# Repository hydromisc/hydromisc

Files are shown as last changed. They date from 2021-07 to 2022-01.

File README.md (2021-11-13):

# Hydromisc

This is a single PCBA with all the necessary I/O to automate a typical
small to mid-size hydroponic grow, controllable over Wi-Fi. It may also
be suitable for aquariums, ponds, or any other biological or chemical
process involving water treatment. Inputs and outputs include:

* 8x 12 V, 1 A outputs, intended for solenoid valves (but usable for other
actuators too)
* 6x 12 V, 0.5 A ouputs, intended for pumps, with current monitoring
* 4x 12 V, 0.25 A outputs, intended for peristaltic dosing pumps, with analog
voltage control
* 2x direct interfaces to a pH probe or other ion-selective electrode
* 2x direct interfaces to an EC (electrical conductivity) probe, reading around 1000 uS
* 2x direct interfaces to a resistive sensor (thermistor, photoresistor,
etc.), reading around 10k
* 2x digital interface to a temperature and humidity sensor
* 2x digital interface to a strain gauge (to measure weight or pressure)

Typical hydroponic practice is to maintain the solution at a target EC and
pH, using EC as a proxy for fertilizer concentration and dosing acid or
(rarely) alkali to adjust pH. I'm using this board now to control injector
pumps in a drain-to-waste system, open-loop with manual adjustment, and
also to maintain closed-loop EC and pH in a recirculating system.

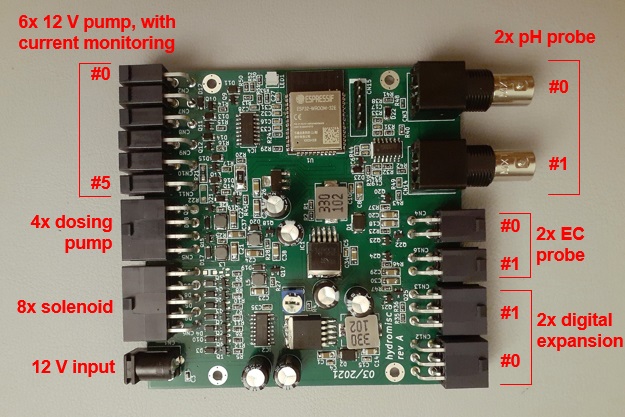
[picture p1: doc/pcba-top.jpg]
all connectors labeled


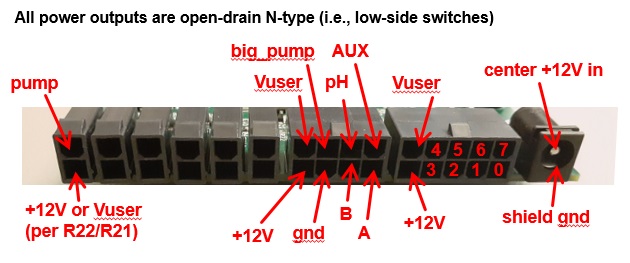
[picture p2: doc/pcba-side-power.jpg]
power side pinout


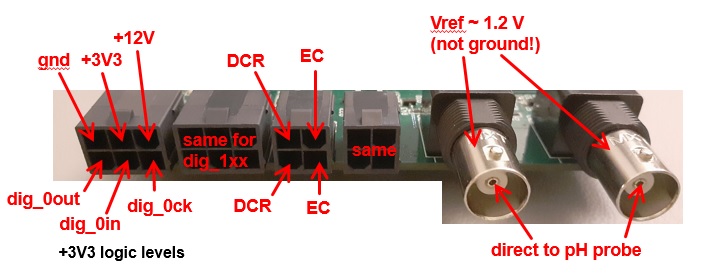
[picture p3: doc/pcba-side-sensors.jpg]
sensor side pinout


## Firmware

The board is managed by an ESP32. Install the
[ESP-IDF](https://github.com/espressif/esp-idf) framework from Espressif,
and build and load the firmware from an ESP-IDF command prompt.

The board is a Wi-Fi client. The name and password for its access point
must be compiled in to the program, in Espressif's usual way, with `idf.py
menuconfig`. The board will automatically get an IP address over DHCP,
so you'll probably want to configure your router or other DHCP server to
assign a static IP based on the MAC address. The MAC address is unique
per board, since that's serialized in the ESP32 module.

The current firmware implements a simple interface to read the sensors
and write the actuators over http. I'm currently sequencing everything with
some shell scripts initiated by cron jobs on a Raspberry Pi, which invoke
curl to command this board. Any device and programming language capable of
making http requests could be used, though.

The outputs are described as "solenoid", "pump", and "dosing pump",
because that's the purpose for which I'm personally using them, and the
present interface is named around that model. They can of course be
used for other types of load too. The software interface is easily
extended if the present commands are inadequate or too confusingly-named.

    $ curl 'http://hydromisc/solenoid?k=3&t=20&'\
    'dosingA=90&dosingB=90&dosingPh=210&dosingAux=0'
    { "result": "solenoiding" }

Solenoid output k is energized for t seconds. For the same period,
the four dosing pumps are also energized, with the respective duty
cycles from 0 (off) to 254 (full on, ~12 VDC). The voltage applied to
the dosing pump is very roughly linear in duty cycle, but both that map
and the map from voltage to speed are quite inexact. If you're closing
the loop (e.g., dosing acid to achieve a particular pH), then this may
not matter, since your control loop will automatically correct that. If
accuracy is important, then the pump should be calibrated, for example
by measuring the amount of liquid dispensed using a graduated cylinder
or weighing scale.

The solenoid output is powered for three seconds after the pumps stop.
This is to avoid closing the solenoid valves with pressure in the system,
since the pumps will continue to operate briefly after losing power. If
the dosing pumps feed directly into a single reservoir, then this and
everything else about the solenoids may be ignored.

    $ curl 'http://hydromisc/pump?k=4&t=15'
    { "result": "pumping" }

Pump output k is energized for t seconds. The measured current (up to about
500 mA) is recorded.

    $ curl 'http://hydromisc/current'
    { "result": "current","current": [ 71, 65, 74, 69, 78, 74, 80, 73, 63,
    73, 65, 68, 74, 64, 60 ] }

The current from the most recent /pump is reported, in units of milliamps
at one sample per second. If this hasn't yet completed, a full-length
trace is reported but future samples are 0.

    $ curl 'http://hydromisc/stop'
    { "result": "stopping" }

All (solenoid, pump, dosing pump) outputs are de-energized immediately.

    $ curl 'http://hydromisc/sensors'
    { "result": "sensors", "ec0": 984, "ec1": 47, "ph0": 41, "ph1": -320,
    "dcr0": 210000, "dcr1": 210000, "temp0": 25.7, "humidity0": 54.0,
    "temp1": -9999.9, "humidity1": -9999.9, "sg0": 0, "sg1": -1 }

All sensors are measured and reported.

The pH electrode voltage is returned in millivolts, and your software
must convert to pH. To a first order, the map from voltage to pH is
linear, with zero volts corresponding to pH = 7.0, and a slope around
59 mV/unit around room temperature (which may be calculated using the
Nernst equation).

You should calibrate by measuring the voltage in two solutions of known
pH (e.g., 4.0 and 6.9), and interpolating linearly between the two. For
example:

    const V69 = 8;      // millivolts in pH 6.9 calibration buffer
    const V40 = -152;   // millivolts in pH 4.0 calibration buffer

    const slope = (V69 - V40)/(6.9 - 4.0);

    let ph = 6.9 + (resp.ph0 - V69)/slope;

Your software must also correct for temperature if desired; though in
typical hydroponic applications, the pH is close enough to neutral that
it doesn't matter too much. To a first order, the slope changes with
temperature but the offset does not, so the tempco is very small when the
output voltage is small.

Other ion-selective electrodes (e.g., for nitrate, potassium, etc.) should
also work with this interface circuit. Consult the electrode documentation
for the calibration procedure, which should be specified in terms of
millivolts from the meter. The reference electrode would need to go to
the BNC shell (Vref ~ 1.2 V), not ground.

EC is returned directly in microsiemens, uS. For example, a resistance
of 1kohm is equal to 1000 uS. Your software must convert based on the
cell dimensions (to convert from uS to uS/cm; a cell constant of 1 cm
is typical so that may be trivial), and also perform any temperature
compensation if desired. If you already have a different EC meter,
then you can use that with a sample of hydroponic solution to transfer
calibration. If not, then you can calibrate in a solution of 1000 mg/L
sodium chloride (table salt), which has conductivity of 2000 uS/cm at
25 degrees Celsius.

In concept, any two wires the right length and distance apart (e.g.,
on the order of 1 cm) could be immersed in solution, and could serve
as your EC electrode. You may prefer to buy a purpose-built electrode,
though. That may have a plastic sheath that protects the electrodes
from mechanical damage with a slit to avoid trapping air bubbles. The
electrode material should also have good electrochemical properties.
Inexpensive electrodes will generally use stainless steel. The most
expensive electrodes will use a thin coating of platinum black, which
reduces error by reducing the series resistance due to electrode
polarization. Either is likely fine in practice.

Electrodes may also be inserted into media, in which case they measure
a product of the solution EC and the media water content. An EC channel
can also be used as a binary liquid level sensor, by placing the
electrodes just below the threshold level. In such use, take care that
the electrodes are far enough apart that surface tension can't hold
a drop of solution even when they aren't immersed.

To measure water (or other) temperature, you can use a thermistor. Some
EC or pH probes will have a thermistor integrated in the probe,
or you can buy one separately. The resistance of that thermistor
(or any other resistive sensor) is returned directly in ohms. Your
software must convert to temperature. For a typical NTC thermistor,
the logarithm of the resistance is proportional to the reciprocal of
absolute temperature. For example:

    // we calibrated at 22 degrees Celsius, and measured 10435 ohms
    const calLogR = Math.log(10435);
    const calTemp = 22;

    // from some random NTC thermistor datasheet, or you could also do a
    // two-point calibration
    const slope = 0.0002578;

    let Tinv = 1/(273 + calTemp) + slope*(Math.log(resp.dcr0) - calLogR);
    let T = 1/Tinv - 273;

I'm also using that interface with a photoresistor to count hours of sun,
though I'm doing a simple binary threshold (to distinguish direct sun
vs. shade) and not a full continuous calibration.

To measure air temperature and humidity, connect an AM2301 on either 2x3
position connector to ground (black), +3V3 (red), and DIG_xOUT (yellow).
Temperature is returned in degrees Celsius, and humidity in percent RH.
A pull-up resistor from red to yellow may be required if the wires are long,
since we otherwise just get the ESP32's on-chip pull-up.

To measure a strain gauge, connect an HX710 to ground, +3V3, DIG_xCK
(SCK), and DIG_xIN (DOUT). The result is returned in raw ADC units,
which you can calibrate to force or pressure with a linear offset and
scale. I use this to measure liquid level with a "bubbler" system,
measuring the hydrostatic pressure in an air-filled tube at the bottom
of the tank. (It's necessary to bubble a slow trickle of air through the
tube, or else tiny leaks will cause it to eventually fill with water; but
since I'm already aerating my tanks, that just takes a tee and a needle
valve. Such systems are common in process industries, crude but cheap
and reliable. My system is okay but not great, since the pressure sensor
has a large tempco. I used an additional AM2301 very close to the sensor
to compensate, but there's still an inch or so worth of residual error.)

You can simultaneously connect an HX710 and an AM2301 to the same
2x3 connector, since they use different data pins.

    $ curl 'http://hydromisc/conf?dosingAPhase=63&dosingBPhase=4032&'\
    'dosingPhPhase=4095&dosingAuxPhase=4095&runBigPump=1'
    { "result": "configured" }

By default, the dosing pumps run continuously during a /solenoid call.
Here they can also be configured to run intermittently, in 100 ms
intervals on a 12-interval (1.2 s) period. The operation of each dosing
pump may be specified here as a bitmap, 12 bits as a decimal number. For
example, the decimal number 63 is equal to 12'b000000111111, so dosing
pump A is on with duty cycle 1/2, 600 ms on followed by 600 ms off. The
decimal number 4032 is equal to 12'b111111000000, so dosing pump B is
also on with duty cycle 1/2 but with opposite phase.

When peristaltic pumps are used as fertilizer injectors, this intermittent
operation can achieve lower injection rates than can be reliably achieved
with low pump voltage (since the transfer characteristic from voltage to
flow varies a lot at low voltage). The phase may be chosen to minimize
risk of mixing before dilution.

By default, the output BIG_PUMP is energized during a /solenoid call. This
may be disabled by setting runBigPump=0.

## Getting Hardware

For the moment, this hardware isn't commercially available in assembled
form. (That may change, since this is open hardware that anyone can build
and sell; I'll add links if and when it does.) You'll therefore have to
buy the bare PCB and parts kit, and assemble yourself. This PCBA has no
leadless or fine-pitch components, so it can be hand-assembled with a
soldering iron and moderate skill.

Note that rev A of the PCB has one major erratum, a missing pull-up on
ESP32_EN, plus some smaller issues that degrade analog performance. I've
corrected these in rev C, which is the head revision in git, but never
actually built and tested that. So it's possible there's still a mistake,
though the risk should be small. Full details of the changes are in
[board/README.md](https://github.com/hydromisc/hydromisc/blob/master/board/README.md).

Total cost to build one board is around:

Item | Cost
----------- | --------------
bare PCB, PCBWay | $30
components, Digi-Key | $60

All connectors are Molex Mini-Fit Jr., a very popular series. It's
possible to solder the cable-end connectors rather than crimping
them, but not recommended. The official crimp tool is expensive. I've used
a third-party "SN-28B", which isn't actually designed for that family
but is cheap and barely adequate, if I crimp first with the largest
die and then again with the middle one.

To program the board, use any USB-to-serial adapter with +3V3 logic levels,
for example an FT232R. Take care that you need access to RTS, which some
such boards and cables don't break out. On CN15, connect:

* ground to ground
* +3V3 to nothing
* USBSER_RX to ESP32_TXD0
* USBSER_TX to ESP32_RXD0
* USBSER_DTR to ESP32_IO0
* USBSER_RTS to ESP32_EN

Program with `idf.py flash` in the usual way. Disconnect digital expansion
devices when programming, since they can interfere.

For complete automated control of EC and pH, you might add:

Item | Cost
----------- | --------------
pH electrode, Yieryi | $15
EC electrode | $15
3x aquarium-type dosing pump | $30
water fill solenoid valve | $15

See my brief
[review of the sensors and actuators now cheaply available on Chinese markets](https://github.com/hydromisc/hydromisc/blob/master/doc/sensors-actuators.md).

Then you might periodically (e.g., minutes to hours) measure EC and pH
with /sensors. You could also monitor solution level, using another EC
electrode positioned high in the tank or using a float switch. The board
has no binary digital inputs, but the DC resistance or EC channels work
with switch contacts too. Then using /solenoid, you could add water,
fertilizer, and acid as required to maintain desired liquid level,
EC and pH.

You would typically aim to keep pH constant, for example with simple
hysteretic (bang-bang) control--add phosphoric if the pH is too high,
or add potassium carbonate if the pH is too low, with a significant
deadband (e.g., 0.5 units) so the acid and alkali don't fight it out
and leave too much potassium phosphate in the solution. In most cases
the alkali would actually be unnecessary, since the natural alkalinity
of the water supplies all necessary pH rise. That's the reason why only
one dosing pump channel is labeled "pH", though the AUX channel could
be used for alkali if desired.

Control of EC is more complicated, since unwanted ions (e.g., sodium
and chloride) will accumulate over time in the solution. So constant EC
probably means rising unwanted ions but falling NPK, and will eventually
result in deficiency. If you maintain constant EC, then you'll need to
change the reservoir often. You can waste less water by allowing slow
rise, though managing that without detailed water analyses is somewhat
uncertain. In all cases, fertilizer should be dosed in a way that doesn't
risk mixing of Part A and Part B before they're fully diluted, to avoid
precipitation (nutrient lockout) from the reaction between calcium ions
and phosphate or sulfate. For example, dose at opposite ends of the tank,
or allow sufficient time to mix between parts.

Of course more complicated automation is possible too. For example, this
board could manage multiple reservoirs simultaneously, or sense EC and
pH both in the reservoir and in returning solution from NFT channels, or
manage fertilizer injectors for a drain-to-waste system. The large number
of inputs and outputs is intended to provide flexibility to interface to
almost any conceivable system's sensors and actuators, with the automated
behavior determined by the software that commands this board.

## Circuit Explanation

Input power is +12 V, which feeds the power outputs directly. It also
feeds a buck converter that makes our +5V, and a buck converter that
makes Vuser, arbitrarily adjustable with a trimpot. An LDO makes +3V3
from +5V, and all our logic runs from that.

The ESP32 is a module with integrated antenna. It would be better for
the antenna tuning if the board outline had a cutout for that, but I
preferred mechanical robustness over antenna range. The ESP32 drives
two 8-bit serial-input, parallel-output shift registers, which function
as GPIO expanders and gate drivers for the pump and solenoid power
FETs. Max current for the solenoid outputs is determined by thermals due
to I^2\*Rdson. I haven't measured that temperature rise, but something
around an amp should be quite safe. Max current for the pump outputs is
determinated by the 2.2 ohm low-side current-sense resistor, and could
be increased by decreasing that.

The dosing pump gates are driven directly by ESP32 PWM outputs. A
series LC makes the negative-ground equivalent of a buck converter
on those outputs, enabling us to drive the dosing pumps not with PWM
but with a programmable DC voltage. This decreases radiated emissions,
and provides something like a constant voltage output as long as the
converter remains in continuous conduction.

The pump outputs return their ground current through a current-sense
resistor, and an ESP32 ADC channel measures the voltage across that. This
enables us to measure pump current. For example, if pump current
is much higher when pumping water than when pumping air, this lets us
measure the volume of water pumped out of a tray by measuring when the
pump current drops. The current can also be used for health monitoring, to
confirm the pump is actually connected and operating with expected load.

A pH electrode develops a voltage around 0 V at pH 7, plus or minus
roughly 59 mV per pH unit at room temperature. Its output impedance may be
many megohms, so we measure that voltage with an electrometer-type opamp,
with femtoamp input current. To mitigate leakage resistance across our
PCB (e.g., due to ionic contamination from flux residue), we surround
the sensitive trace with a driven shield held at the same voltage as that
sensitive node. I've seen no trouble due to leakage even without cleaning
flux, though I live in a dry climate and it would be better to clean that.

Since the pH electrode voltage may be positive or negative and we don't
have a negative supply, we connect its "ground" to a 1.2 V reference. This
means that any electrical connection between our circuit ground and
the solution being measured will result in an incorrect measurement,
though the shunt regulator that generates that rail can survive a short
to ground without damage. The shield of the BNC connectors is 1.2 V,
not ground. As long as the board is powered from an isolated power supply
(for example, a typical mains-operated power brick), no further attention
should be required; but take care not to de-isolate it, for example by
attaching board ground to any metal that touches the solution.

Even with DC isolation, a significant 60 Hz (or 50 Hz) component may
be present on the pH probe voltage. If this saturates the front-end
amplifier, then no subsequent low-pass could recover the correct DC
voltage. We address this with a capacitor across the pH probe. The
resulting low-pass time constant is poorly-controlled, since it's a
function of the probe output resistance.  That's fine in practice though,
since pH shouldn't change significantly over any timescale faster than
minutes.

We pull both sides of the EC electrode up to +3V3 through 1k
resistors, so they both rest at +3V3 with respect to circuit ground, 0 V
differential. To measure EC, we pull one side to ground through an n-FET,
and then measure the voltage of the other, making a voltage divider
between the known 1k and the unknown resistance under test. We then
repeat the process for the other side, restoring zero DC voltage across
the electrode to avoid polarization. The EC electrode is also AC-coupled
through 22 uF ceramic capacitors, guaranteeing zero DC voltage even if
the software misbehaves or the resistors don't perfectly match and, more
importantly, presenting high imepedance at DC so the EC electrode doesn't
short out a pH electrode immersed in the same sample cup. Assuming EC
around 2 mS/cm and cell constant around 1 cm, we get a high-pass time
constant around 4 ms, which is much slower than our measurement period
of ~500 us. Electrolytic capacitors can't be used for that AC-coupling,
since the leakage current is too high.

A similar approach may be used to measure EC with almost
any microcontroller and no additional components beyond the
reference resistors and AC-coupling capacitors, by configuring that
microcontroller's I/O pin as an output low to ground it. I chose to use
the external FETs here because I'd run out of microcontroller pins, and
because the lower and more consistent Rdson improves accuracy at high EC
(since that appears in series with the resistance under test).

## Information Security

None whatsoever. Use this only behind a firewall (like a typical
residential NAT router), on a network with trusted users only. If you
need remote access, expose it through a properly-secured jump box or VPN,
not directly.

## Warranty and Life Safety

THERE IS NO WARRANTY FOR THIS SOFTWARE OR HARDWARE, TO THE EXTENT
PERMITTED BY APPLICABLE LAW. WE PROVIDE THE SOFTWARE OR HARDWARE "AS IS"
WITHOUT WARRANTY OF ANY KIND, EITHER EXPRESSED OR IMPLIED, INCLUDING,
BUT NOT LIMITED TO, THE IMPLIED WARRANTIES OF MERCHANTABILITY AND FITNESS
FOR A PARTICULAR PURPOSE.

DO NOT USE THIS SOFTWARE OR HARDWARE IN SITUATIONS WHERE ITS FAILURE COULD
RESULT IN DANGER TO HUMAN LIFE. For example, don't dose concentrated acid
and rely on correct operation of this board to safely dilute it--instead
dose a higher volume of less concentrated acid, or use safer chemistry
(monopotassium phosphate, etc.). Also think carefully about the risk of
overflowing water, dead plants or fish, and other damage, and don't rely
on software to prevent it.

## License

The firmware is licensed under the GPLv3 or later. The legal framework
for open hardware is poorly-established, but you may build and sell, give
away, or otherwise transfer any number of hydromisc boards, provided that:

* any software loaded on the board is free software (as defined by
any OSI-approved license), and that software is not intended primarily
as a bootloader or other tool to load, program, or otherwise enable use
of non-free software; and

* you do not falsely claim ownership of the design, or any affiliation
with this project beyond your permission to build boards per above.

## Next steps

For now, this project is useful only to people with sufficient programming
skill to build and load the firmware, and to use the http interface
above. For future, it would be nice to:

* Integrate with existing control software (Mycodo, home automation packages,
etc.)

* And/or, add logic on the ESP32 itself for timed irrigations and
closed-loop dosing based on measured pH and EC, to allow this board
to work standalone with no need for the network except for initial
configuration. Firmware to log and graph (as a web page) sensors over
time would also be helpful in standalone use.

* Add a friendly mode to configure Wi-Fi settings, since those currently
must be compiled in. For example, if some combination of pins is jumpered
at startup, appear as a Wi-Fi access point to which the user can connect
and provide the real access point name and password. Then save those
credentials in flash, and use them after reset.

* Clean up how concurrency is managed in the firmware. The present code
seems to work, but it's a lazy hack that's hard to analyze for races.

I might eventually do some of that work myself, but I have limited time
and welcome other contributors. Please feel free to use GitHub issues to
discuss potential new features or anything else.

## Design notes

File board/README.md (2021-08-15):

There are three revisions of the PCB:

* rev A - I built this, and it works except that I forgot the pull-up on
ESP32_EN. Solder a 10k resistor from ESP32_EN to +3V3 (for example, near
CN15), or else the ESP32 module won't start when the programmer is
disconnected.

* rev B - This adds the missing pull-up, as R54. It also adds R55 and
R56 from Vuser to ground, enabling use of LM2596 parts from vendors
(e.g. ON Semi) that have much higher leakage current than the National/TI
original, up to 2 mA! A lightly-loaded Vuser may lose regulation when
Ileakage\*Rpulldown > Vsetpoint, and that R was previously just the
feedback divider.

* rev C - This adds capacitors to create a passive low-pass on the pH
inputs, improving 60 Hz (or 50 Hz) rejection and thus reducing noise
e.g. when the probe is connected with long wires. It also changes the
series resistors between Vref and the BNC shield from 1k to zero-ohm,
since the shunt regulator that makes Vref can survive a short-circuit
to ground with no problem and that resistance worsens noise performance.

The head revision in git is rev C; but I've never actually built this
revision, so it's possible there's still a mistake. That risk should be
very small, though. I'll amend this note if/when someone builds rev C
and reports back.

This is a two-layer board, designed to PCBWay's standard design rules.
Almost any vendor should be able to make this, though. 1.6mm thick,
1 oz/ft^2 copper.

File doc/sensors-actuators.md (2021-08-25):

# Sensors and Actuators for Automated Hydroponics

An automated hydroponic system measures nutrient solution pH, EC, and
other quantities, and adds calculated amounts of water, fertilizer,
and pH up/down in response. The sensors and actuators required for that
are available from suppliers like Atlas Scientific or Hanna Instruments,
but at rather high prices.

They're also now available on Chinese markets, typically with poor
documentation and murky provenance but far cheaper. This is a summary
of my experiences (mostly good, occasionally bad) with those products.

I've included market links, but those may rot quickly. The listings are
usually from random small trading companies, and the actual manufacturer
is sometimes unclear. You may be able to match pictures or description
words to find new listings if necessary.

## pH Electrodes

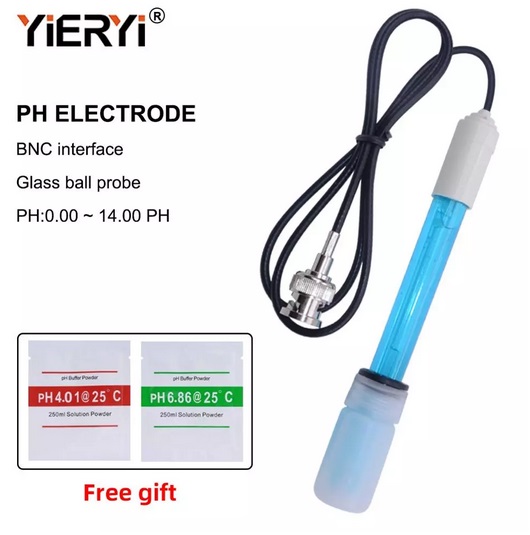
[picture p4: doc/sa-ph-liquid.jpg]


<https://www.aliexpress.com/item/32813510050.html>

Liquid-filled pH electrode from Yieryi. It comes with calibration
standards, little sachets of powder that make pH = 4.0 and 6.9 buffers
when dissolved in distilled water. Settling is fast, seconds. The
measurement has drifted by a maximum of 0.15 units from initial
calibration over 8 months of use, continuously immersed in nutrient
solution except when calibrating.

No obvious way to refill, so this is a consumable, probably with life of
1-2 years. Failure will probably exhibit as either drifting calibration
or very slow settling. The electrode comes wet, with a small plastic cup
of liquid pressed over the end, and should never be allowed to dry out.
Ideally the probe should be stored in special storage solution (e.g.,
3 mol/L potassium chloride), but nutrient solution or tap water are
better than dry. Don't store in distilled water, which may accelerate aging.

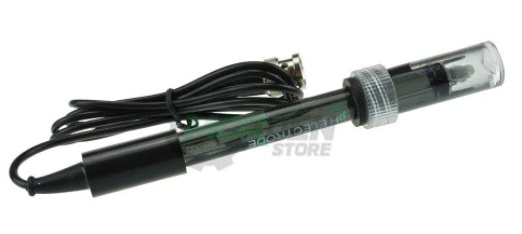
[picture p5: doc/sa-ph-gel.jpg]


<https://www.aliexpress.com/item/4001075011664.html>

Gel-filled pH electrode from Yieryi. Very similar performance to the
liquid-filled, maybe a little slower to settle.

These pH electrodes interface directly to the hydromisc board. The listing
above includes an amplifier board suitable for interfacing to any micro's
ADC pin, though. Any electrode should work with any interface circuit,
with no special steps (beyond calibration, which is always required).

## EC Electrodes

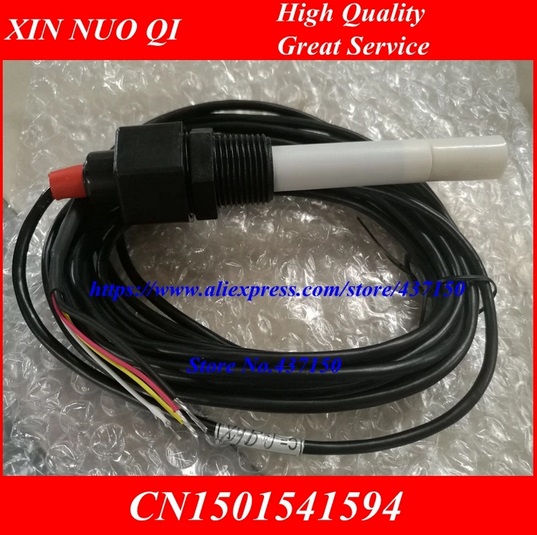
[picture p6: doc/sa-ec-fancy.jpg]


<https://www.aliexpress.com/item/32818088740.html>

Fancy electrode, with platinum black on the contacts. This presents a
large effective surface area, and should decrease the rate of electrode
polarization and corresponding error resistance in series; though with
proper interface electronics I'd expect that to be negligible regardless
of contact material. The nominal cell constant is 1 cm, which means
e.g. that if the solution EC is 2 mS/cm, then the electrode will present
a conductance of 2 mS, which is a resistance of 500 &Omega;. The exact
cell constant is handwritten on a tag on the cable, presumably from a
factory calibration and test. No degradation in accuracy was observed
after 8 months continuously immersed.

This probe includes a temperature sensor, an NTC thermistor with resistance
around 10k around room temperature. The EC measurement itself is insensitive
to temperature, but the conversion factor between fertilizer concentration
and EC varies with temperature (by ~1.4%/&deg;C for me, but this will vary
with your nutrients and source water).

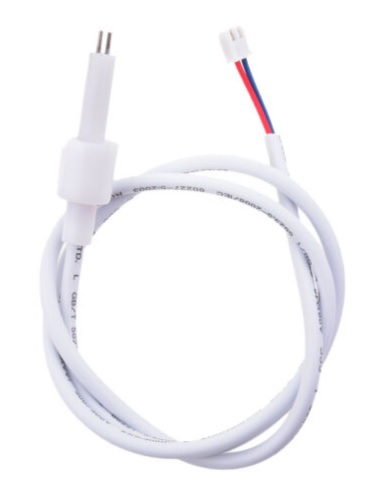
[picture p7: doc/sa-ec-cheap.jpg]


<https://www.ebay.com/itm/372674667406>

Cheap electrode, just stainless steel. Cell constant is also 1 cm, no
temperature sensor. You could make the same thing from some stainless
wire and RTV silicone; this just saves you the trouble of building and
figuring out the cell constant. Seems fine, though I tested only briefly.

These EC electrodes interface directly to the hydromisc board. To interface
to a standard micro, use two resistors and two capacitors as described
in the hydromisc circuit explanation.

## Nitrate Electrode - Not Successful

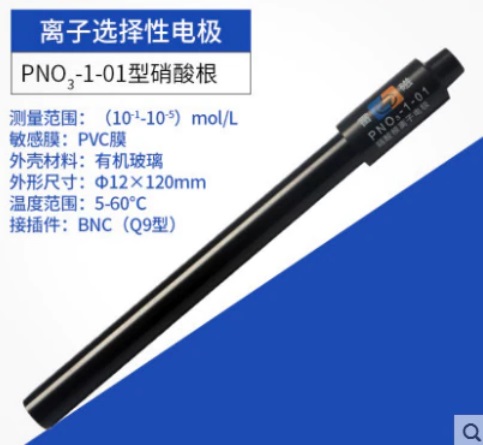
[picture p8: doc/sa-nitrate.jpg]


<https://www.aliexpress.com/item/1005002783499630.html>

If I translate the instructions correctly, this is intended for use with
a calomel reference electrode made by the same company. I didn't want
calomel anywhere near my food, so I used a silver chloride reference
electrode instead.

Unfortunately the first electrode I bought behaved like an open circuit. I
eventually hacksawed it open. I found no fill solution, and no evidence
(e.g., dried salts) that any fill solution had ever been present. That seems
like a manufacturing defect.

I bought a second electrode, which came with fill solution leaking around
the polymer membrane at the tip. That one behaved like a short circuit,
I suspect with current leaking along the same path that the fill solution
was. That seems like a second, different manufacturing defect. I may
try reworking that to seal the leak, but so far my experience has not
been good.

It's hard to believe the factory quality could be so bad, but the two
electrodes were from two different traders and I'm not sure what
else could be wrong. I'll probably try again with a different, more
expensive brand.

## Peristaltic Dosing Pump

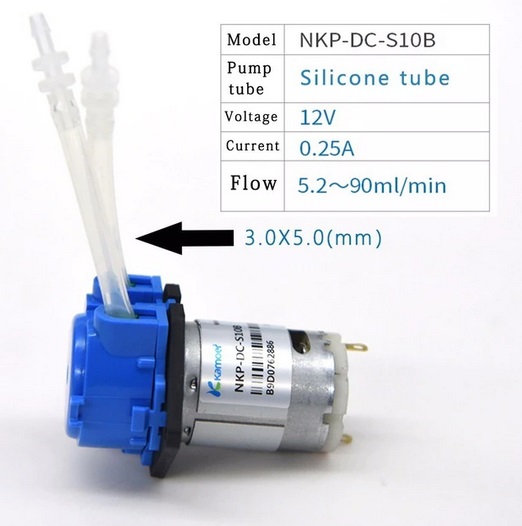
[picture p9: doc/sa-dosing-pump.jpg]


<https://www.aliexpress.com/item/4001162555100.html>

<https://www.ebay.com/itm/353153163498>

Often used for dosing aquarium chemicals. The blue head snaps onto
the motor, and the housing of the blue head is itself held together by
snaps. The motor shaft presses against three rollers inside the head. The
small-diameter motor shaft turns quickly. The rollers pressed against the
shaft are much larger-diameter, so they turn slowly. The rollers press
against the silicon tubing, pumping the liquid peristaltically. Since
the liquid only ever touches the silicone tube, you can pump acids or
salt solutions without risk of corrosion.

In aquarium use these pumps just dump straight in to the tank, and they
can dump straight in to a hydroponic reservoir too. They can also develop
considerable pressure though (easily ~30 psi), and flow rate doesn't
vary strongly with that back-pressure. This makes them also suitable
for use as fertilizer injectors.

Speed matches pretty well (to within ~5%) between pumps, so that e.g. two
pumps can be relied upon to dose roughly equal volumes of fertilizer
Part A and Part B. Matching is best at full speed, and gets worse when
operating at lower voltage for lower speed. If lower speed is desired,
then it's better to slowly pulse the motors (e.g., 200 ms on, 800 ms off)
than to decrease the voltage or do high-speed PWM.

The tubing will eventually wear, though after 8 months mine still
looks new.  It's easily replaced if necessary, just with standard
silicone tubing of the desired diameter. I reworked some pumps with
smaller-diameter tubing for lower dosing rate, and that worked as
expected. If the new tubing is bigger then the head may be hard to
assemble, and if it's smaller then you may need to shim it (e.g., with
some packing tape on the inside of the blue housing).

## Air Pressure Sensor

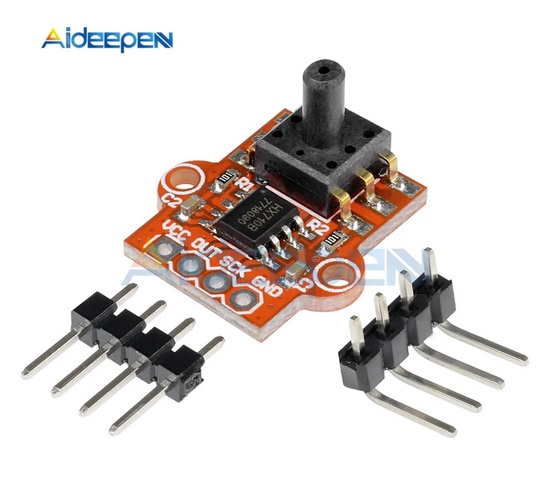
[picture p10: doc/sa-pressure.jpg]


<https://www.aliexpress.com/item/33054432260.html>

I use this for my reservoir level gauge, measuring the hydrostatic
pressure in an air-filled tube at the bottom of the reservoir. To stop
the tube from slowly filling with water (due to leaks, air dissolving
in water, etc.), a slow trickle of air is bubbled through, from the same
aquarium pump used to aerate. This kind of "bubbler" level gauge is
commonly used in process industries.

Temperature coefficient is the dominant error, on the order of 1 cm
water column per &deg;C. The HX710B integrates a temperature sensor,
but a brief experiment looked noisy. I used a AM2301 placed very close
to the pressure sensor. Accuracy after linear temperature correction is
better than 1 cm, over a daily temperature swing around 20 &deg;C.

## Air Temperature and Humidity Sensor

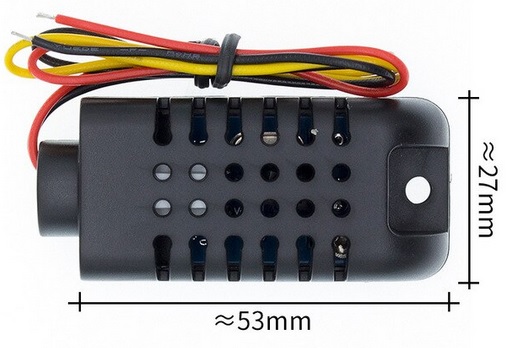
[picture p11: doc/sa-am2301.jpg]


<https://www.aliexpress.com/item/32769460765.html>

Very popular, 0.1 &deg;C resolution, easy digital interfacing.

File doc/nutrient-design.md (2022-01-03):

# What elements does a plant need to grow?

In this article, we'll briefly discuss the chemistry behind plant
nutrition. We'll then use my
[calculator](https://hydromisc.github.io/hydromisc/doc/nutrient-calculator.html)
to design a complete two-part hydroponic fertilizer customized for my
hard tap water, blending from individual salts. We'll send a sample of
that for laboratory analysis, and review those results.

Plants need 16 elements[^1] to grow. Of those, carbon, hydrogen and oxygen
are available from water and air. This leaves 13 essential elements that
must be supplied by fertilizer or soil:

<blockquote>
N, P, K, Ca, Mg, S, Fe, Cu, Mn, Zn, B, Mo, Cl
</blockquote>

The most important are nitrogen, phosphorus, and potassium. By convention,
fertilizers are labeled with three numbers representing that percent
N-P-K[^2]. Soil or soil-like potting mix will often provide enough of
the remaining elements that no further attention is required, allowing
many growers to ignore everything except that N-P-K.

But in hydroponics, there's no soil. This is true both in pure hydroponic
methods like DWC, where the roots are directly in water, and in inert
media like rockwool that provide mechanical support but no fertility. So
hydroponic fertilizers must be complete, including all essential
elements. The plants take the elements up as ions. For the metals
that's usually just the corresponding cation (e.g., K as K+, Ca as Ca++),
but for the other elements it may be a more complex ion (e.g. N as NH4+
or NO3-, P as PO4---). A cation and an anion together form a salt,
and fertilizers are blended from salts to achieve the desired element
ratio. For example, potassium nitrate contributes both potassium 
and nitrogen.

Complete fertilizers are readily available pre-blended. Liquid
concentrates are sold for amateur growers, for example the General
Hydroponics Flora series. These are easy to use, since they can be
measured by volume and don't need shaking to dissolve; but they're also
rather bulky and expensive per unit of fertility, since they're mostly
water. Commercial growers typically buy powdered solid nutrients, measure
them by weight, and dissolve them into liquid concentrates themselves.

For example, Masterblend 4-18-38[^3] tomato fertilizer is readily
available, and despite the name is at least roughly suitable for
growing almost any plant species. It contains almost all the essential
elements, but no calcium. This is because in a concentrated solution,
the calcium will precipitate against phosphates or sulfates, dropping
out as a sediment at the bottom of the tank that's unavailable to the
plants. Complete fertilizers should always come in at least two parts[^4],
one with the calcium and one with the sulfates and phosphates.

That Masterblend product also contains very little magnesium[^5], and
thus requires additional magnesium sulfate. Kits are readily available
with that Masterblend (or another similar almost-complete fertilizer),
calcium nitrate, and magnesium sulfate in the correct ratio. I've been
growing for about a year with:

<blockquote>
0.4 g/L Masterblend<br>
0.4 g/L Ca(NO3)2<br>
0.2 g/L MgSO4
</blockquote>

For some mature plants, I use a stronger solution in the same ratio. This
Masterblend is a very common choice among amateur growers. It's working
relatively well for me, but not ideally:

1. My water has quite high alkalinity[^6], with initial pH around
8.5. Ideal pH for most plants is around 6.0. So I use a large amount of
phosphoric acid[^7] to bring my pH down, which adds adds more phosphorus
than the plants need to my nutrient profile. I'd like to decrease the
phosphorus in the fertilizer to offset, but I can't remove the phosphorus
already blended into the Masterblend.

2. Beyond the effect on the plants, the extra phosphate also precipitates
against calcium in the nutrient solution. That calcium phosphate
precipitate tends to clog drippers, and generally make a mess. So
for that reason too, I'd like to decrease the phosphate, and slightly
decrease the calcium.

3. As my reservoir empties, I top it up with new solution. This
means that any ions not taken up by the plants will concentrate, and
eventually become toxic. Sodium and chloride are the usual offenders
here, though others are possible too. Masterblend 4-18-38 gets some of its
potassium from potassium chloride, perhaps because tomatoes are relatively
salt-tolerant and KCl is cheaper than other sources of potassium. To get
rid of that accumulated chloride, I need to periodically dump my reservoir
and restart fresh. That works, but it's a nuisance and a waste of water.

## Designing a custom nutrient profile

So I wanted to switch to a custom nutrient profile without these problems.
To start, I used the 
[calculator](https://hydromisc.github.io/hydromisc/doc/nutrient-calculator.html)
to look at my existing profile. Note that 0.4 g/L = 400 mg/L, which is 400 ppm
since the density of water is around 1 kg/L.



The calculator gives me a breakdown by element of the overall nutrient
profile. As a special case, total nitrogen, ammonium nitrogen, and nitrate
nitrogen are tracked separately. In soil, nitrifying bacteria will convert
ammonium to nitrate, so the form in which nitrogen is applied doesn't
matter much.  In hydroponics these bacteria aren't necessarily present;
so plants see the fertilizer's nitrate:ammonium ratio directly, and too
much ammonium can be toxic to the plants. That ratio also affects pH
trend, since uptake by the plant effectively swaps an NH4+ ion for an H+
(decreasing pH), but swaps an NO3- for an HCO3- (increasing pH). Typical
hydroponic fertilizers provide about 90% of the nitrogen as nitrate,
the rest as ammonium.

Chlorine is an essential element, but it's required in such small amounts
and present naturally in such large amounts that deficiency is practically
impossible. There's therefore no need to deliberately add any, so it's
not considered in that breakdown.

Starting from my existing profile, the changes I wanted to make were to:

1. Remove all chloride.

2. Reduce the calcium by about 35 ppm, since my water utility's website
indicates that my tap water should provide at least that much.

3. Reduce the magnesium by about 12 ppm, since my tap water also
provides that.

4. Reduce the phosphorus to zero, since the acid used to adjust pH
provides more than enough.

5. Reduce the copper, zinc, and manganese, for fear they'd concentrate
and become toxic in the same way as sodium or chloride[^8].

To make these changes, I edited the element concentrations in the "goal"
line of the calculator accordingly.

## Converting to a blend of fertilizer salts

I then set all the ingredient inputs to zero, and un-checked
all the ingredients containing chloride so the goal seek algorithm
couldn't use them. I pressed the goal seek button, which returned
a tentative recipe:

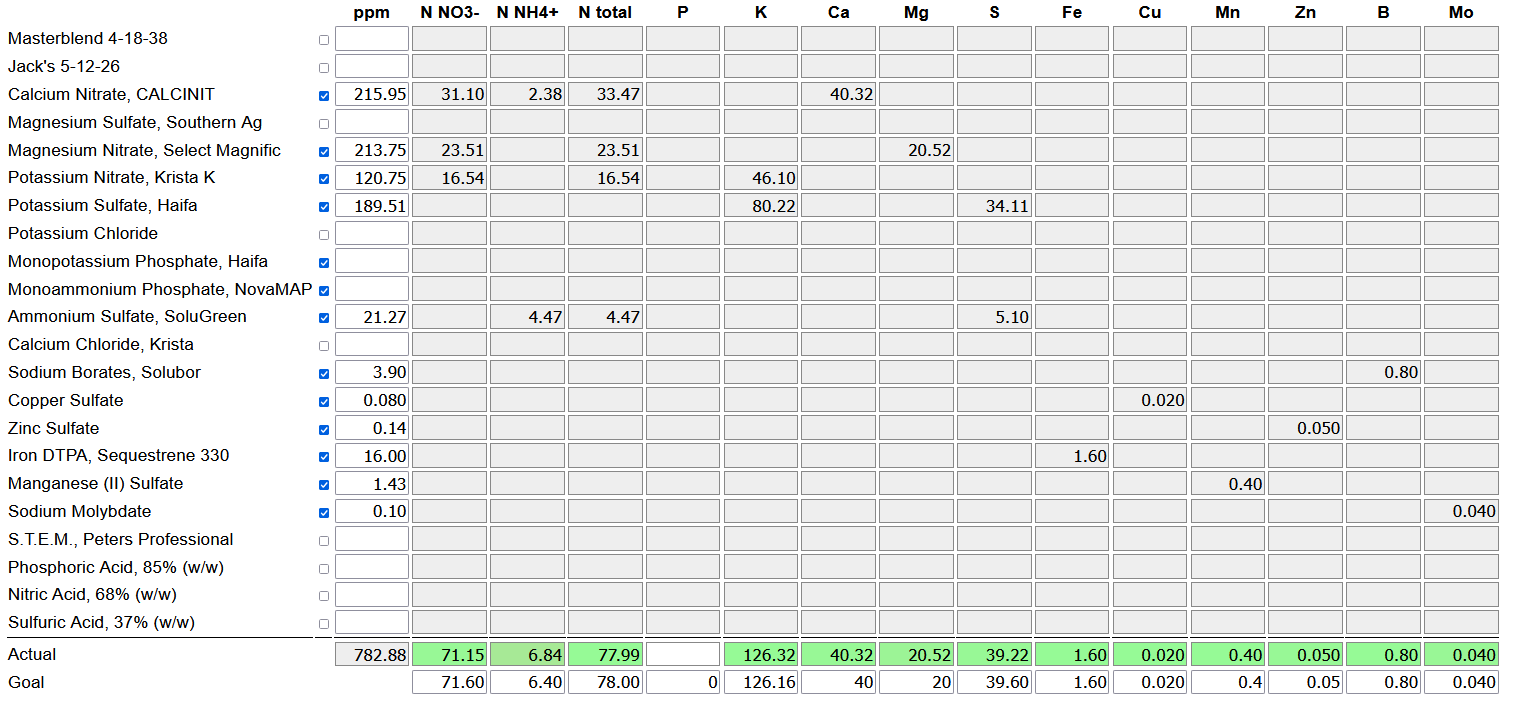
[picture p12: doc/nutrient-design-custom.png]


From there I rounded to the final recipe, and split the ingredients
into two parts, in order to avoid precipitation of calcium phosphates or
sulfate as discussed above. I mixed the following concentrates:

##### Micronutrient sodium stock solution:
<blockquote>
16.0 g Sodium Borate<br>
0.4 g Sodium Molybdate<br>
983.6 g Water
</blockquote>

##### Micronutrient sulfate stock solution:
<blockquote>
0.8 g Copper Sulfate<br>
1.3 g Zinc Sulfate<br>
14 g Manganese Sulfate<br>
100 g Phosphoric Acid, 75% w/w<br>
883.9 g Water
</blockquote>

##### Part A[^9]:
<blockquote>
120 g Potassium Nitrate<br>
190 g Potassium Sulfate<br>
20 g Ammonium Sulfate<br>
250 g micronutrient sodium stock<br>
100 g micronutrient sulfate stock<br>
water to make 1 gal
</blockquote>

##### Part B:
<blockquote>
220 g Calcium Nitrate<br>
220 g Magnesium Nitrate<br>
16 g Iron DTPA<br>
water to make 1 gal
</blockquote>

I'm working mostly in metric here, but I made a gallon of each concentrate
since I'm in the USA and can easily obtain gallon jugs.

The micronutrients are mixed in separate stock solutions, to save the
effort of re-weighing them for each batch of nutrients. All solutions
with micronutrient sulfates are acidified, since without that the copper,
zinc and manganese will precipitate as the hydroxide or carbonate at
high pH. (Even if no carbonate is added to a solution, it will absorb
CO2 from air.) Most fertilizers would get that acidification naturally
from the monopotassium phosphate (which is an acid salt), but here none
is present. Sulfuric acid would be better, but I had phosphoric at hand
and it seems to work.

The stock solution measurements are given by weight and not volume,
since I have an accurate scale but no accurate liquid measures. The final
Part A and Part B concentrates are made up to a specified weight/volume,
not weight/weight, since they'll be dosed by volume.

These concentrates should provide the specified ppm of each element at a
volume ratio of 1:220, since 220 gal ~ 1000 L. In practice my [automated
dosing system](https://github.com/hydromisc/hydromisc) dilutes using
peristaltic pumps, which aren't precisely calibrated so I just watch the
EC[^10]. This means that I don't exactly know the absolute concentration,
but the relative element ratios are fixed.

## Laboratory analysis

I sent a sample of nutrient solution for analysis by A&L Great Lakes
Laboratories, as a quality control check to confirm (a) that I hadn't made
a careless mistake while blending, (b) that my suppliers had actually
sent me the right chemicals, and (c) that my tap water actually met the
specifications on my local utility's website. I paid $45, and I got the
following back:

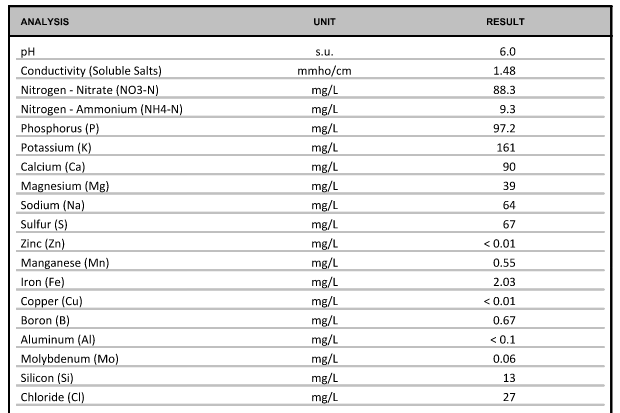
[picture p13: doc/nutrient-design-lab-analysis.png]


This includes the contributions of both my nutrients and the source
water. It's mostly as expected, a little stronger than my design
but everything scaled up ratiometrically[^11]. P is very high[^12],
but it was even higher with the Masterblend. I'm not sure why the Cu
and Zn ended up below their limit of detection; I was concerned that
something was still precipitating, but I don't see any sediment. I'm
hoping their limit of detection was just slightly higher than the claimed
0.01 ppm. Sodium and chloride are both high, but I'm pretty sure that's
just my source water and not impurities in my fertilizer salts.

So I'm basically pleased with my recipe. I'm growing a few plants as a
final test, and if those continue to look good I'll switch all my systems
to the new recipe within a couple months. I don't suggest copying this
recipe directly, since your water and growing goals are likely different
from mine; but my intent here is to provide a rough template for the
process and considerations required to develop a fertilizer customized
for your own needs.

*First published Nov 2021, updated Jan 2022:* The original version of this
article used citric acid to acidify the nutrients and stock solution.
This worked, but I got filamentous solids after about a month, which
I suspect were fungi eating the citrate. I've switched to phosphoric
acid and seen no more trouble. The test grows went well, with good yield
and no obvious deficiencies. All my previous grows with the Masterblend
showed rising EC with time, while this one showed falling, implying an
improved match between the ions in the solution and the ions taken up
by the plants. I'm now running my complete automated system with these
nutrients and pleased with the growth.

[^1]: Or 17 counting nickel for urease, and certain rare plant species
need additional elements. It's almost never necessary to consider any
elements beyond those 16, though.

[^2]: Actually it's percent N directly, but it's percent equivalent P2O5
and K2O. This doesn't mean the fertilizers actually contain phosphorus
pentoxide or potassium oxide; the percent is just the concentration
of those compounds to achieve the same percent P and K. This is an
unfortunate piece of historical confusion, and some fertilizer vendors
now include the actual percent P and K elsewhere on the label too.

[^3]: So 4% N, 18% P2O5 equivalent, 38% K2O equivalent.

[^4]: Some vendors provide one-part nutrients intended for use with
hard water, where the source water supplies all the calcium. These
can work, but risk calcium deficiency if the water isn't hard enough.
Some vendors also provide solid one-part nutrients including calcium,
but these may be tricky or impossible to dissolve fully.

[^5]: Nothing fundamentally stops the blend from including more
magnesium, since there's no precipitation problem like with the
calcium. Their goal might have been to allow growers with source water
high in magnesium to decrease the magnesium sulfate dose to offset.

[^6]: Note that in water chemistry, alkalinity doesn't just mean
"high pH". Very roughly, alkalinity is a measure of the total amount
of strong acid required to bring the pH down to a particular level,
which is determined by various factors including the carbonate buffer
system. Two solutions could have the same pH, but different alkaliniity.

[^7]: Sulfuric acid or nitric acid would have a more favorable effect
on the nutrient profile, but they're more and much more dangerous
respectively. Citric acid would have no effect on the nutrient profile,
but it breaks down upon contact with the plants or reservoir
microbiota, becoming ineffective as quickly as within hours.

[^8]: Papers studying plant response to those micronutrients generally
show a small increase in yield as those increase, followed by a steep
decrease after the toxic level. So running at optimal levels seems like it
trades a small benefit (if we get the dose exactly right) against the
risk of a big problem (if we overshoot). That didn't seem worth
it for me.

[^9]: The literature seems inconsistent on whether the part with the
calcium is Part A or Part B; I've seen it both ways.

[^10]: The solution electrical conductivity, in units like microsiemens
per cm, uS/cm. This is used as a rough indication of the concentration of
nutrient solutions, since that EC is roughly linearly proportional to the
total dissolved content of ionic stuff. The scale factor varies with the
specific ions, though. Instruments to measure EC are readily available,
starting at just a few dollars. Many EC meters will also read out in
"ppm", but they're actually just multiplying EC by a constant scale factor
that's not exactly correct unless you're measuring pure NaCl solution
(for those using 500 ppm/(mS/cm)) or pure KCl (for 700). This means the
"true ppm" as calculated from the actual mg/L dosed and the "EC meter
ppm" will be different, and the "EC meter ppm" may also be different
with different meters. That's all pretty confusing, so I prefer to work
in EC directly.

[^11]: For example, target total nitrogen was 78 ppm and they measure
88 + 9 = 97 ppm, 24% higher. Target potassium was 126 ppm and they
measure 161 ppm, 28% higher, so a similar ratio.

[^12]: A professional would use sulfuric or nitric acid, but I don't
want that in my apartment. It's also possible to remove the alkalinity
in the water by reverse osomosis instead of neutralizing it with acid,
and that would solve the problem completely. Household RO systems
work, but generate perhaps three gallons of waste per gallon purified.
Agricultural RO systems use pumps to achieve much higher pressure and
thus better waste ratio, but they're designed for users well above
my scale.

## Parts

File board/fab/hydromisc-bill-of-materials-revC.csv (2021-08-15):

hydromisc bill of materials, rev C, Aug 2021
Qty | Reference Designators | Value | Description | Digi-Key P/N
16 | C1, C2, C8, C14, C18, C20, C21, C22, C23, C24, C26, C29, C30, C34, C37, C38, | 22u | capacitor, 1206, MLCC, 16 V, X5R | 1276-2728-1-ND
18 | C3, C4, C5, C10, C15, C16, C17, C19, C25, C27, C28, C31, C32, C33, C35, C36, C39, C40, | 100n | capacitor, 0603, MLCC, 25 V, X7R | 1276-1006-1-ND
6 | C6, C7, C9, C11, C12, C13, | 220u | capacitor, electrolytic, 25 V, through-hole radial | 399-6112-ND
1 | CN1, |  | connector, DC power, coaxial, 2.1 mm | CP-102AH-ND
6 | CN2, CN7, CN8, CN9, CN10, CN11, |  | connector, Mini-Fit Jr., 2x1 | WM16206-ND
2 | CN3, CN14, |  | connector, BNC, right angle | WM5514-ND
2 | CN4, CN16, |  | connector, Mini-Fit Jr., 2x2 | WM16295-ND
1 | CN5, |  | connector, Mini-Fit Jr., 2x4 | WM17269-ND
1 | CN6, |  | connector, Mini-Fit Jr., 2x5 | WM17284-ND
2 | CN12, CN13, |  | connector, Mini-Fit Jr., 2x3 | WM17089-ND
1 | CN15, |  | header, 0.100", 6 position | S1022EC-06-ND
2 | D1, D2, |  | diode, schottky, SMB | 641-SS34B-HFCT-ND
21 | D3, D4, D5, D6, D7, D8, D9, D10, D11, D12, D13, D14, D15, D16, D17, D18, D19, D20, D21, D22, D23, |  | diode, schottky, SOD-123 | 1655-1929-1-ND
2 | IC1, IC3, |  | LM2596, buck controller with integrated switch, adjustable | LM2596DSADJR4GOSCT-ND
2 | IC2, IC4, |  | 74HC594, octal serial in parallel out shift register | 74HC594DCT-ND
1 | IC5, |  | LMC6024, opamp with ultra-low input current | 296-35434-1-ND
1 | IC6, |  | voltage reference, 1.2 V | 576-2571-1-ND
1 | IC7, |  | AZ1117I, low dropout linear regulator, 3.3 V | AZ1117IH-3.3TRG1DICT-ND
2 | L1, L2, | 33u | inductor, 4.1 A | 308-2500-1-ND
4 | L3, L4, L5, L6, | 220u | inductor, 280 mA | 490-LQH44PH221MPRLCT-ND
1 | LED1, |  | LED, yellow | 1497-1052-ND
25 | Q1, Q2, Q3, Q4, Q5, Q6, Q7, Q8, Q9, Q10, Q11, Q12, Q13, Q14, Q15, Q16, Q17, Q18, Q19, Q20, Q21, Q22, Q23, Q24, Q25, |  | n-FET, SOT-23 | DMG2302UK-7DICT-ND
3 | R1, R33, R34, | 33k | resistor, 0603, 1% | CR0603-FX-3302ELFCT-ND
5 | R2, R24, R31, R32, R54, | 10k | resistor, 0603, 1% | CR0603-FX-1002ELFCT-ND
1 | R3, | 10k | trimpot, through-hole | 478-601030-ND
40 | R4, R5, R6, R7, R8, R9, R10, R11, R12, R13, R14, R15, R16, R17, R18, R20, R23, R25, R26, R27, R28, R29, R30, R35, R36, R37, R38, R39, R40, R42, R44, R45, R46, R47, R50, R51, R52, R53, R55, R56, | 1k | resistor, 0603, 1% | CR0603-FX-1001ELFCT-ND
1 | R19, | 2.2 | resistor, 2010, 5% | RMCF2010JT2R20CT-ND
1 | R21, | zerohm | resistor, 1206, zero-ohm | 311-0.0ERTR-ND
2 | R41, R43, | zerohm | resistor, 0603, zero-ohm | 311-0.0HRTR-ND
1 | R22, |  | do not populate
2 | R48, R49, |  | do not populate
1 | U1, |  | ESP32 module with integrated antenna, 16 MB | 1965-ESP32-WROOM-32E(16MB)CT-ND

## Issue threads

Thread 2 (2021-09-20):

Use for Koi Pond and integration in Homeassistant

DirkTas67, 2021-09-20:
Hello,

I'm very interested in this project to manage my koi pond, however I would like it to integrate in Homeassistant.
I suspect every function runs on the esp32 and the 'rest'of the components are there to let input and output function correctly, just correct me if i'm wrong.

I ordered the pcb and the parts and i have most of the thing allready here except for a few parts I still have to receive from digikey.

I don't know if you know the esphome project at https://esphome.io/, with this you can probably do most of the things you allready did in your code, but esphome devices can simply be added in homeassistant.

The great advantage of ESPHome is that the device can run independatly.

Maybe you can look into it?

Regards,
Dirk

hydromisc, 2021-09-20:
Cool, and let us know how the build goes. I don't keep an aquarium or pond, but the basic requirements (measure EC, pH, temperature, etc., dose chemicals, control pumps) seem very similar.

I'm aware of the ESPHome project, though not deeply familiar. I believe that out of the box, it could interface to some parts of the I/O that I'm using (e.g., the pH sensor, which to the ESP32 is just an analog voltage input, or the AM230x temperature and humidity sensors), but not others (e.g., the EC sensors, which require multiple measurements properly sequenced in time, or, significantly, all the pump/solenoid outputs since they're through a shift register functioning as a GPIO expander).

So I believe some additions to the ESPHome firmware would be required to properly support this board. I have no time for that work myself, but I believe it could be quite valuable if anyone wanted to take that on (or otherwise integrate with home automation software), definitely the preferred programming approach for a lot of people.

Closed 2023-05-20.

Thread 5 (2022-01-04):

Can I add a monitor?

vichelian, 2022-01-04:
Can an external small monitor be connected?

hydromisc, 2022-01-04:
There's no firmware support for that now, but you could connect an I2C display on one of the digital expansion connectors. Probably easier just to monitor over the network though, or mount a cheap phone/tablet someplace if you want a stationary display.

Closed 2022-01-04.

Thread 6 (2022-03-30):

Some components unavailable with high lead time.

Relys, 2022-03-30:
Hey, I'm looking to build one of these and noticed that a few components are unavailable on digikey due to the chip shortage. Are there any alternatives I could use?

1724480008
SS34B-HF
LM2596DSADJR4G
LM4041CYM3-1.2-TR
AZ1117IH-3.3TRG1
DMG2302UK-7

hydromisc, 2022-03-31:
1724480008 - 0039301081
SS34B-HF - any Schottky diode with same or greater voltage and current rating
LM2596DSADJR4G - Mouser
LM4041CYM3-1.2-TR - Mouser
AZ1117IH-3.3TRG1 - NCV1117ST33T3G
DMG2302UK-7 - any logic-level n-FET with same or greater voltage and current rating

Please double-check the new part numbers yourself too. Let me know how the build goes, or if you want me to double-check your replacement Schottky/FET.

godzillachan, 2023-01-10:
Came across this project during my search on hydroponics controllers and I am interested in producing small quantities of these boards.  Can we get in touch?

hydromisc, 2023-01-10:
This is open hardware, so please feel free to build. If you have questions then you can just ask here or on reddit (/u/lathyrus_long).

Closed 2023-05-20.

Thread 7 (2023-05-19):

Not a bug…

G4KCM, 2023-05-19:
Don’t think GitHub supports a THANK YOU but I would just like to express my appreciation to the developer as this is a really nice controller.  Couple of points for those who may be interested.  I used an ESP32 with an external antenna which is useful if you have a poor WiFi signal where you want to place it.  I also found that the latest v5 version of the Expressif toolchain throws a lot of errors.  Rather than mess with the (very eloquent) code I reverted to v4.2.1. which was released circa the time this project was released into GitHub and thus far seems all ok (just awaiting an AM2301) to complete the check out.

I’m interfacing to it via node-red and Home Assistant.

A very professionally designed and documented piece of work, thank you once again!

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

hydromisc, 2023-05-20:
Thanks, and your build looks good. You might post some pictures on /r/hydroponics once you assemble that with the pumps and such, since they tend to like that kind of stuff. The Home Assistant interface might also be of interest to others, if you wanted to publish that.

Closed 2023-07-06.

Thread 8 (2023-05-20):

AM2301 Issue

G4KCM, 2023-05-20:
It seems that the AM2301 doesn't work on either input it just returns 0.0 for both temperature and humidity.
I'm wondering if this is also related to the version of the compiler?  Can't think why looking at the code but I must admit I can't get my head around it.  I suspect it might be that the timing is adrift as I see on inspection the device is an AM2301A not AM2301.

I wonder if you could let me have a functioning binary to test and/or advise which version of the ESP-idf was used in ther meantime I will see if I can get an origional AM2301/DHT21 somewhere.

Thanks

hydromisc, 2023-05-20:
I built with `ESP-IDF v4.1-dirty`, though I'm surprised that would matter. My binary wouldn't work for you, since the Wi-Fi credentials are compiled in. Note that you may need an external pull-up resistor (from the red wire to yellow) if the wires are long. If it still doesn't work, then can you scope the yellow wire?

G4KCM, 2023-05-20:
> I built with `ESP-IDF v4.1-dirty`, though I'm surprised that would matter. My binary wouldn't work for you, since the Wi-Fi credentials are compiled in. Note that you may need an external pull-up resistor (from the red wire to yellow) if the wires are long. If it still doesn't work, then can you scope the yellow wire?

Hi, appreciate you getting back to me…  I don’t think the ESP-IDF version will matter either.  First thing I tried was a pull-up and that made no difference also with a scope on the data line the sensor is sending back data but it returns 0.0 for both temperature and humidity.  I think the reason is that the ‘new’ AM2301 that I have purchased is actually labelled as an AM2301A the insides of the housing are not the same as the ‘original’ AM2301 as it looks like they have got something like and AHT10 inside and and some firmware to translate to the single comms line.  In fact the AM2301A and an AM2302 I have are identical inside so I suspect that’s the issue.   I have just ordered some ‘original’ AM2301 from AliExpress 🤞

Just one question, I see there is a dht.c library that supports the AM230x devices included within the esp-idf. Is there a specific reason that you didn’t use that?  I may have a play using that library to see if it will read the AM2301A devices whilst I wait for the slow boat from China.  Thanks again for a great bit of work.

hydromisc, 2023-05-21:
I have no experience with anything except the original AM2301, so I guess that could be it. I wasn't aware of that dht.c until you mentioned it now, seems worth a try.

Closed 2023-07-06.

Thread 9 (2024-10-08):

PCB help

yfaykya, 2024-10-08:
Hi,
Been a few years since I created a PCB. Do I just zip up the board directory?
Is there a bom for board components ?
Thanks!!

hydromisc, 2024-10-08:
There's a BOM and already-zipped board files in

https://github.com/hydromisc/hydromisc/tree/master/board/fab

Closed 2024-10-08.

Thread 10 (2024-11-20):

What version of esp-idf is required?

yfaykya, 2024-11-20:
Hi - What version of idf is required? I am using :
```
:~/DEV/hydromisc/esp32$ idf.py --version
ESP-IDF v5.3.1

```

Also which side of CN15 is ground?

Thanks for a great project!!

yfaykya, 2024-11-20:
Warning/errors from 5.3.1 compile :
```

 98%] Building C object esp-idf/wifi_provisioning/CMakeFiles/__idf_wifi_provisioning.dir/proto-c/wifi_scan.pb-c.c.obj
[ 98%] Building C object esp-idf/wifi_provisioning/CMakeFiles/__idf_wifi_provisioning.dir/proto-c/wifi_ctrl.pb-c.c.obj
[ 98%] Building C object esp-idf/wifi_provisioning/CMakeFiles/__idf_wifi_provisioning.dir/proto-c/wifi_constants.pb-c.c.obj
[ 98%] Building C object esp-idf/wifi_provisioning/CMakeFiles/__idf_wifi_provisioning.dir/src/scheme_softap.c.obj
[ 98%] Linking C static library libwifi_provisioning.a
[ 98%] Built target __idf_wifi_provisioning
[ 98%] Building C object esp-idf/main/CMakeFiles/__idf_main.dir/main.c.obj
In file included from /home/osulliv/DEV/hydromisc/esp32/main/main.c:41:
/home/osulliv/DEV/esp-idf/components/driver/deprecated/driver/periph_ctrl.h:7:2: warning: #warning driver/periph_ctrl.h header is no longer used, and will be removed in future versions. [-Wcpp]
    7 | #warning driver/periph_ctrl.h header is no longer used, and will be removed in future versions.
      |  ^~~~~~~
In file included from /home/osulliv/DEV/hydromisc/esp32/main/main.c:42:
/home/osulliv/DEV/esp-idf/components/driver/deprecated/driver/timer.h:16:2: warning: #warning "legacy timer group driver is deprecated, please migrate to driver/gptimer.h" [-Wcpp]
   16 | #warning "legacy timer group driver is deprecated, please migrate to driver/gptimer.h"
      |  ^~~~~~~
In file included from /home/osulliv/DEV/hydromisc/esp32/main/main.c:43:
/home/osulliv/DEV/esp-idf/components/driver/deprecated/driver/adc.h:19:2: warning: #warning "legacy adc driver is deprecated, please migrate to use esp_adc/adc_oneshot.h and esp_adc/adc_continuous.h for oneshot mode and continuous mode drivers respectively" [-Wcpp]
   19 | #warning "legacy adc driver is deprecated, please migrate to use esp_adc/adc_oneshot.h and esp_adc/adc_continuous.h for oneshot mode and continuous mode drivers respectively"
      |  ^~~~~~~
In file included from /home/osulliv/DEV/hydromisc/esp32/main/main.c:44:
/home/osulliv/DEV/esp-idf/components/esp_adc/deprecated/include/esp_adc_cal.h:17:2: warning: #warning "legacy adc calibration driver is deprecated, please migrate to use esp_adc/adc_cali.h and esp_adc/adc_cali_scheme.h" [-Wcpp]
   17 | #warning "legacy adc calibration driver is deprecated, please migrate to use esp_adc/adc_cali.h and esp_adc/adc_cali_scheme.h"
      |  ^~~~~~~
/home/osulliv/DEV/hydromisc/esp32/main/main.c: In function 'config_gpio':
/home/osulliv/DEV/hydromisc/esp32/main/main.c:143:25: error: 'GPIO_PIN_INTR_DISABLE' undeclared (first use in this function); did you mean 'GPIO_INTR_DISABLE'?
  143 |     io_conf.intr_type = GPIO_PIN_INTR_DISABLE;
      |                         ^~~~~~~~~~~~~~~~~~~~~
      |                         GPIO_INTR_DISABLE
/home/osulliv/DEV/hydromisc/esp32/main/main.c:143:25: note: each undeclared identifier is reported only once for each function it appears in
/home/osulliv/DEV/hydromisc/esp32/main/main.c:199:5: warning: 'ADC_ATTEN_DB_11' is deprecated [-Wdeprecated-declarations]
  199 |     adc1_config_channel_atten(ADC_PH_0_SENSE, ADC_ATTEN_DB_11);
      |     ^~~~~~~~~~~~~~~~~~~~~~~~~
In file included from /home/osulliv/DEV/esp-idf/components/driver/deprecated/driver/adc_types_legacy.h:8,
                 from /home/osulliv/DEV/esp-idf/components/driver/deprecated/driver/adc.h:15:
/home/osulliv/DEV/esp-idf/components/hal/include/hal/adc_types.h:51:5: note: declared here
   51 |     ADC_ATTEN_DB_11 __attribute__((deprecated)) = ADC_ATTEN_DB_12,  ///<This is deprecated, it behaves the same as `ADC_ATTEN_DB_12`
      |     ^~~~~~~~~~~~~~~
/home/osulliv/DEV/hydromisc/esp32/main/main.c:200:5: warning: 'ADC_ATTEN_DB_11' is deprecated [-Wdeprecated-declarations]
  200 |     adc1_config_channel_atten(ADC_PH_1_SENSE, ADC_ATTEN_DB_11);
      |     ^~~~~~~~~~~~~~~~~~~~~~~~~
/home/osulliv/DEV/esp-idf/components/hal/include/hal/adc_types.h:51:5: note: declared here
   51 |     ADC_ATTEN_DB_11 __attribute__((deprecated)) = ADC_ATTEN_DB_12,  ///<This is deprecated, it behaves the same as `ADC_ATTEN_DB_12`
      |     ^~~~~~~~~~~~~~~
/home/osulliv/DEV/hydromisc/esp32/main/main.c:201:5: warning: 'ADC_ATTEN_DB_11' is deprecated [-Wdeprecated-declarations]
  201 |     adc1_config_channel_atten(ADC_EC_0_SENSE, ADC_ATTEN_DB_11);
      |     ^~~~~~~~~~~~~~~~~~~~~~~~~
/home/osulliv/DEV/esp-idf/components/hal/include/hal/adc_types.h:51:5: note: declared here
   51 |     ADC_ATTEN_DB_11 __attribute__((deprecated)) = ADC_ATTEN_DB_12,  ///<This is deprecated, it behaves the same as `ADC_ATTEN_DB_12`
      |     ^~~~~~~~~~~~~~~
/home/osulliv/DEV/hydromisc/esp32/main/main.c:202:5: warning: 'ADC_ATTEN_DB_11' is deprecated [-Wdeprecated-declarations]
  202 |     adc1_config_channel_atten(ADC_EC_1_SENSE, ADC_ATTEN_DB_11);
      |     ^~~~~~~~~~~~~~~~~~~~~~~~~
/home/osulliv/DEV/esp-idf/components/hal/include/hal/adc_types.h:51:5: note: declared here
   51 |     ADC_ATTEN_DB_11 __attribute__((deprecated)) = ADC_ATTEN_DB_12,  ///<This is deprecated, it behaves the same as `ADC_ATTEN_DB_12`
      |     ^~~~~~~~~~~~~~~
/home/osulliv/DEV/hydromisc/esp32/main/main.c:203:5: warning: 'ADC_ATTEN_DB_11' is deprecated [-Wdeprecated-declarations]
  203 |     adc1_config_channel_atten(ADC_DCR_SENSE, ADC_ATTEN_DB_11);
      |     ^~~~~~~~~~~~~~~~~~~~~~~~~
/home/osulliv/DEV/esp-idf/components/hal/include/hal/adc_types.h:51:5: note: declared here
   51 |     ADC_ATTEN_DB_11 __attribute__((deprecated)) = ADC_ATTEN_DB_12,  ///<This is deprecated, it behaves the same as `ADC_ATTEN_DB_12`
      |     ^~~~~~~~~~~~~~~
/home/osulliv/DEV/hydromisc/esp32/main/main.c:207:5: warning: 'ADC_ATTEN_DB_11' is deprecated [-Wdeprecated-declarations]
  207 |     esp_adc_cal_characterize(ADC_UNIT_1, ADC_ATTEN_DB_11, ADC_WIDTH_BIT_12,
      |     ^~~~~~~~~~~~~~~~~~~~~~~~
/home/osulliv/DEV/esp-idf/components/hal/include/hal/adc_types.h:51:5: note: declared here
   51 |     ADC_ATTEN_DB_11 __attribute__((deprecated)) = ADC_ATTEN_DB_12,  ///<This is deprecated, it behaves the same as `ADC_ATTEN_DB_12`
      |     ^~~~~~~~~~~~~~~
/home/osulliv/DEV/hydromisc/esp32/main/main.c: At top level:
/home/osulliv/DEV/hydromisc/esp32/main/main.c:443:8: error: unknown type name 'xQueueHandle'
  443 | static xQueueHandle timer_tick_queue;
      |        ^~~~~~~~~~~~
/home/osulliv/DEV/hydromisc/esp32/main/main.c: In function 'timer_tick_task':
/home/osulliv/DEV/hydromisc/esp32/main/main.c:451:23: warning: passing argument 1 of 'xQueueReceive' makes pointer from integer without a cast [-Wint-conversion]
  451 |         xQueueReceive(timer_tick_queue, &evt, portMAX_DELAY);
      |                       ^~~~~~~~~~~~~~~~
      |                       |
      |                       int
In file included from /home/osulliv/DEV/esp-idf/components/freertos/esp_additions/include/freertos/idf_additions.h:21,
                 from /home/osulliv/DEV/esp-idf/components/freertos/FreeRTOS-Kernel/include/freertos/FreeRTOS.h:1533,
                 from /home/osulliv/DEV/esp-idf/components/esp_event/include/esp_event.h:12,
                 from /home/osulliv/DEV/esp-idf/components/esp_wifi/include/esp_wifi.h:55,
                 from /home/osulliv/DEV/hydromisc/esp32/main/main.c:25:
/home/osulliv/DEV/esp-idf/components/freertos/FreeRTOS-Kernel/include/freertos/queue.h:825:41: note: expected 'QueueHandle_t' {aka 'struct QueueDefinition *'} but argument is of type 'int'
  825 | BaseType_t xQueueReceive( QueueHandle_t xQueue,
      |                           ~~~~~~~~~~~~~~^~~~~~
/home/osulliv/DEV/hydromisc/esp32/main/main.c: In function 'timer_tick_isr':
/home/osulliv/DEV/hydromisc/esp32/main/main.c:516:5: error: implicit declaration of function 'timer_spinlock_take'; did you mean 'timer_tick_task'? [-Werror=implicit-function-declaration]
  516 |     timer_spinlock_take(TIMER_GROUP_0);
      |     ^~~~~~~~~~~~~~~~~~~
      |     timer_tick_task
/home/osulliv/DEV/esp-idf/components/freertos/FreeRTOS-Kernel/include/freertos/queue.h:1134:31: warning: passing argument 1 of 'xQueueGenericSendFromISR' makes pointer from integer without a cast [-Wint-conversion]
 1134 |     xQueueGenericSendFromISR( ( xQueue ), ( pvItemToQueue ), ( pxHigherPriorityTaskWoken ), queueSEND_TO_BACK )
      |                               ^~~~~~~~~~
      |                               |
      |                               int
/home/osulliv/DEV/hydromisc/esp32/main/main.c:522:5: note: in expansion of macro 'xQueueSendFromISR'
  522 |     xQueueSendFromISR(timer_tick_queue, &evt, NULL);
      |     ^~~~~~~~~~~~~~~~~
/home/osulliv/DEV/esp-idf/components/freertos/FreeRTOS-Kernel/include/freertos/queue.h:1203:52: note: expected 'QueueHandle_t' {aka 'struct QueueDefinition *'} but argument is of type 'int'
 1203 | BaseType_t xQueueGenericSendFromISR( QueueHandle_t xQueue,
      |                                      ~~~~~~~~~~~~~~^~~~~~
/home/osulliv/DEV/hydromisc/esp32/main/main.c:524:5: error: implicit declaration of function 'timer_spinlock_give' [-Werror=implicit-function-declaration]
  524 |     timer_spinlock_give(TIMER_GROUP_0);
      |     ^~~~~~~~~~~~~~~~~~~
/home/osulliv/DEV/hydromisc/esp32/main/main.c: In function 'config_timer_tick':
/home/osulliv/DEV/hydromisc/esp32/main/main.c:529:22: warning: assignment to 'int' from 'QueueHandle_t' {aka 'struct QueueDefinition *'} makes integer from pointer without a cast [-Wint-conversion]
  529 |     timer_tick_queue = xQueueCreate(10, sizeof(int));
      |                      ^
/home/osulliv/DEV/hydromisc/esp32/main/main.c:544:52: error: 'TIMER_BASE_CLK' undeclared (first use in this function)
  544 |     timer_set_alarm_value(TIMER_GROUP_0, TIMER_0, (TIMER_BASE_CLK / (16*10)));
      |                                                    ^~~~~~~~~~~~~~
cc1: some warnings being treated as errors
make[2]: *** [esp-idf/main/CMakeFiles/__idf_main.dir/build.make:76: esp-idf/main/CMakeFiles/__idf_main.dir/main.c.obj] Error 1
make[1]: *** [CMakeFiles/Makefile2:5599: esp-idf/main/CMakeFiles/__idf_main.dir/all] Error 2
make: *** [Makefile:136: all] Error 2

```

hydromisc, 2024-11-21:
Thanks, and looks like I built with 4.1. I don't immediately see the cause for the breakage, but if you fix it then I'd merge (or you could just downgrade of course). Pin 1 of CN15 (the programming connector) is ground.

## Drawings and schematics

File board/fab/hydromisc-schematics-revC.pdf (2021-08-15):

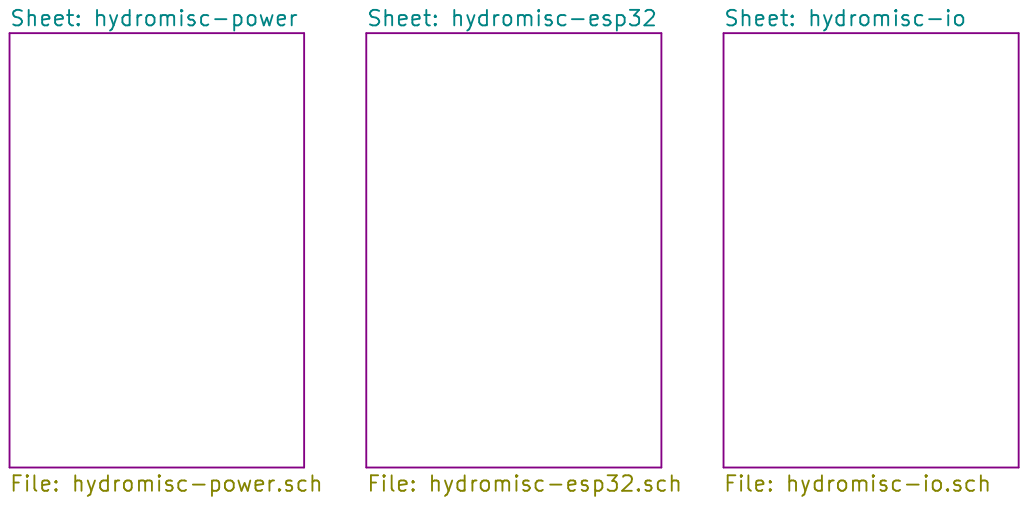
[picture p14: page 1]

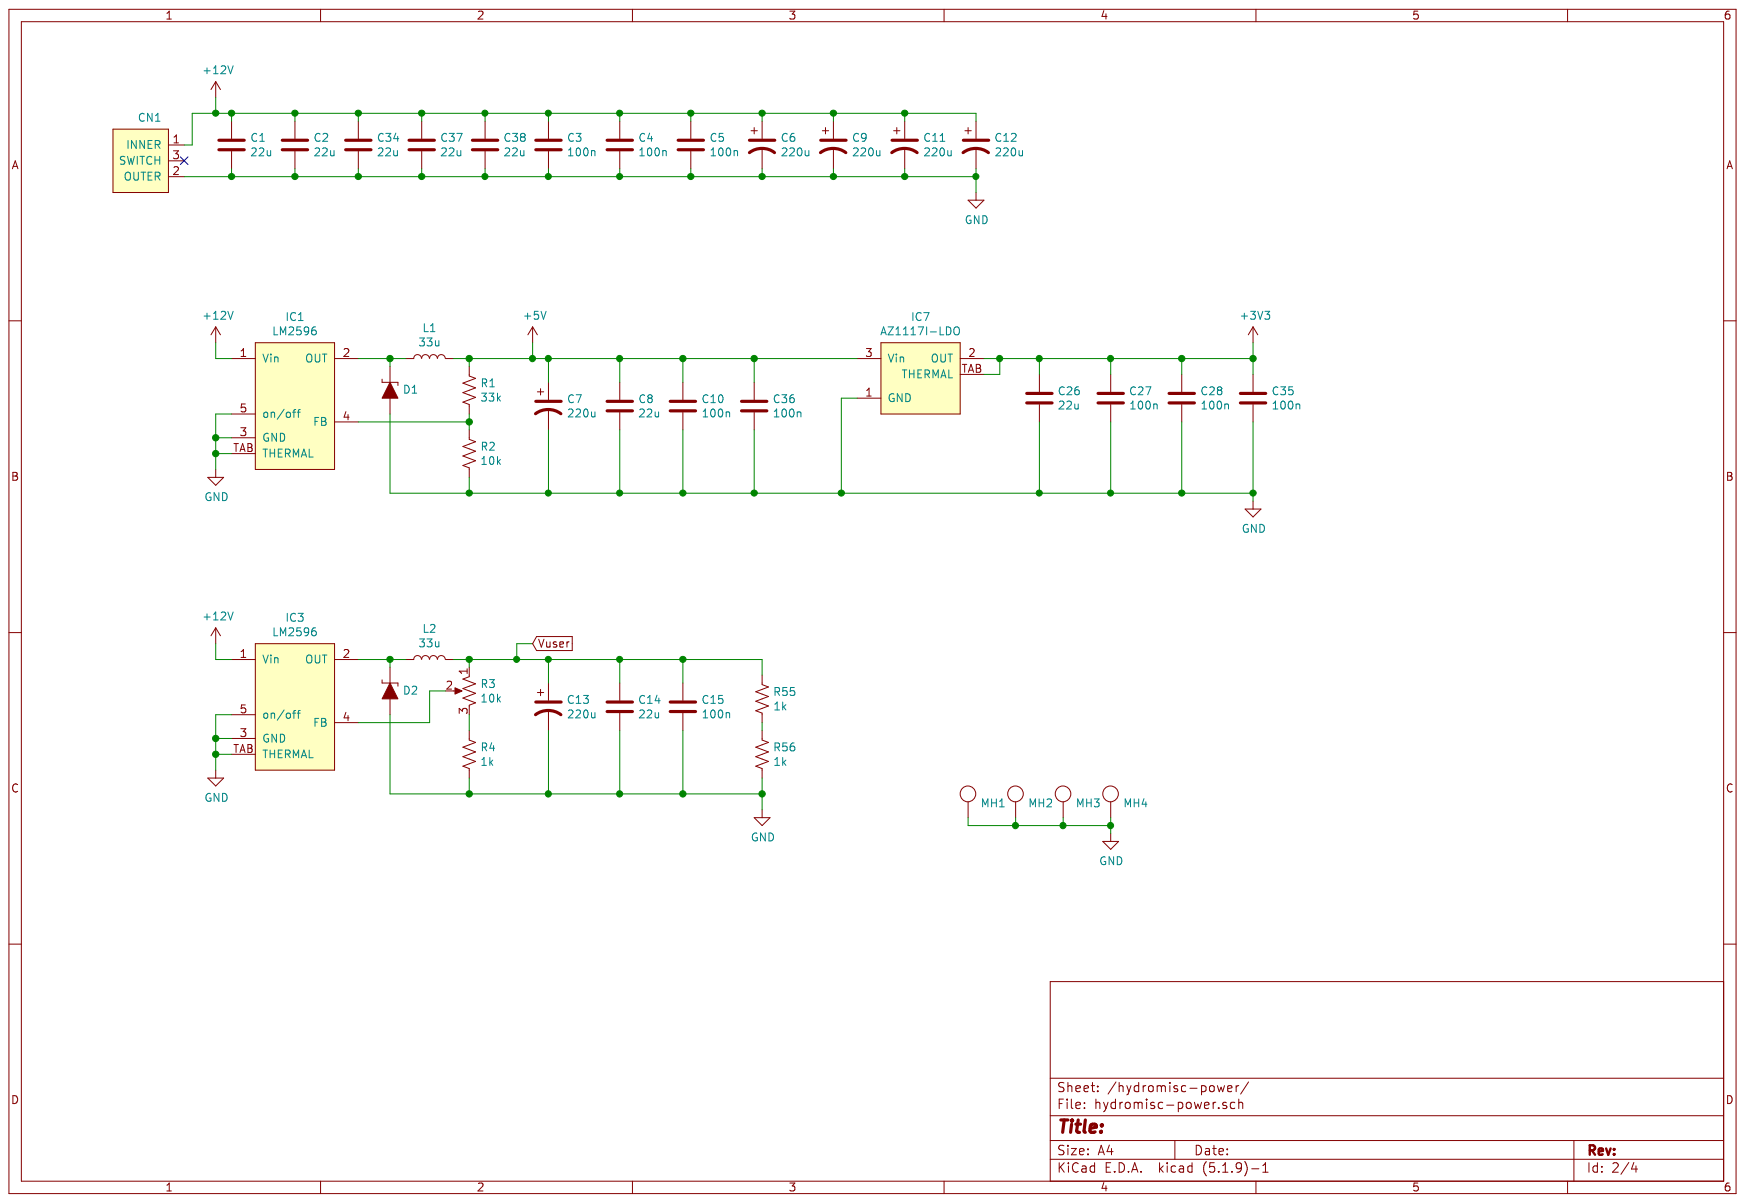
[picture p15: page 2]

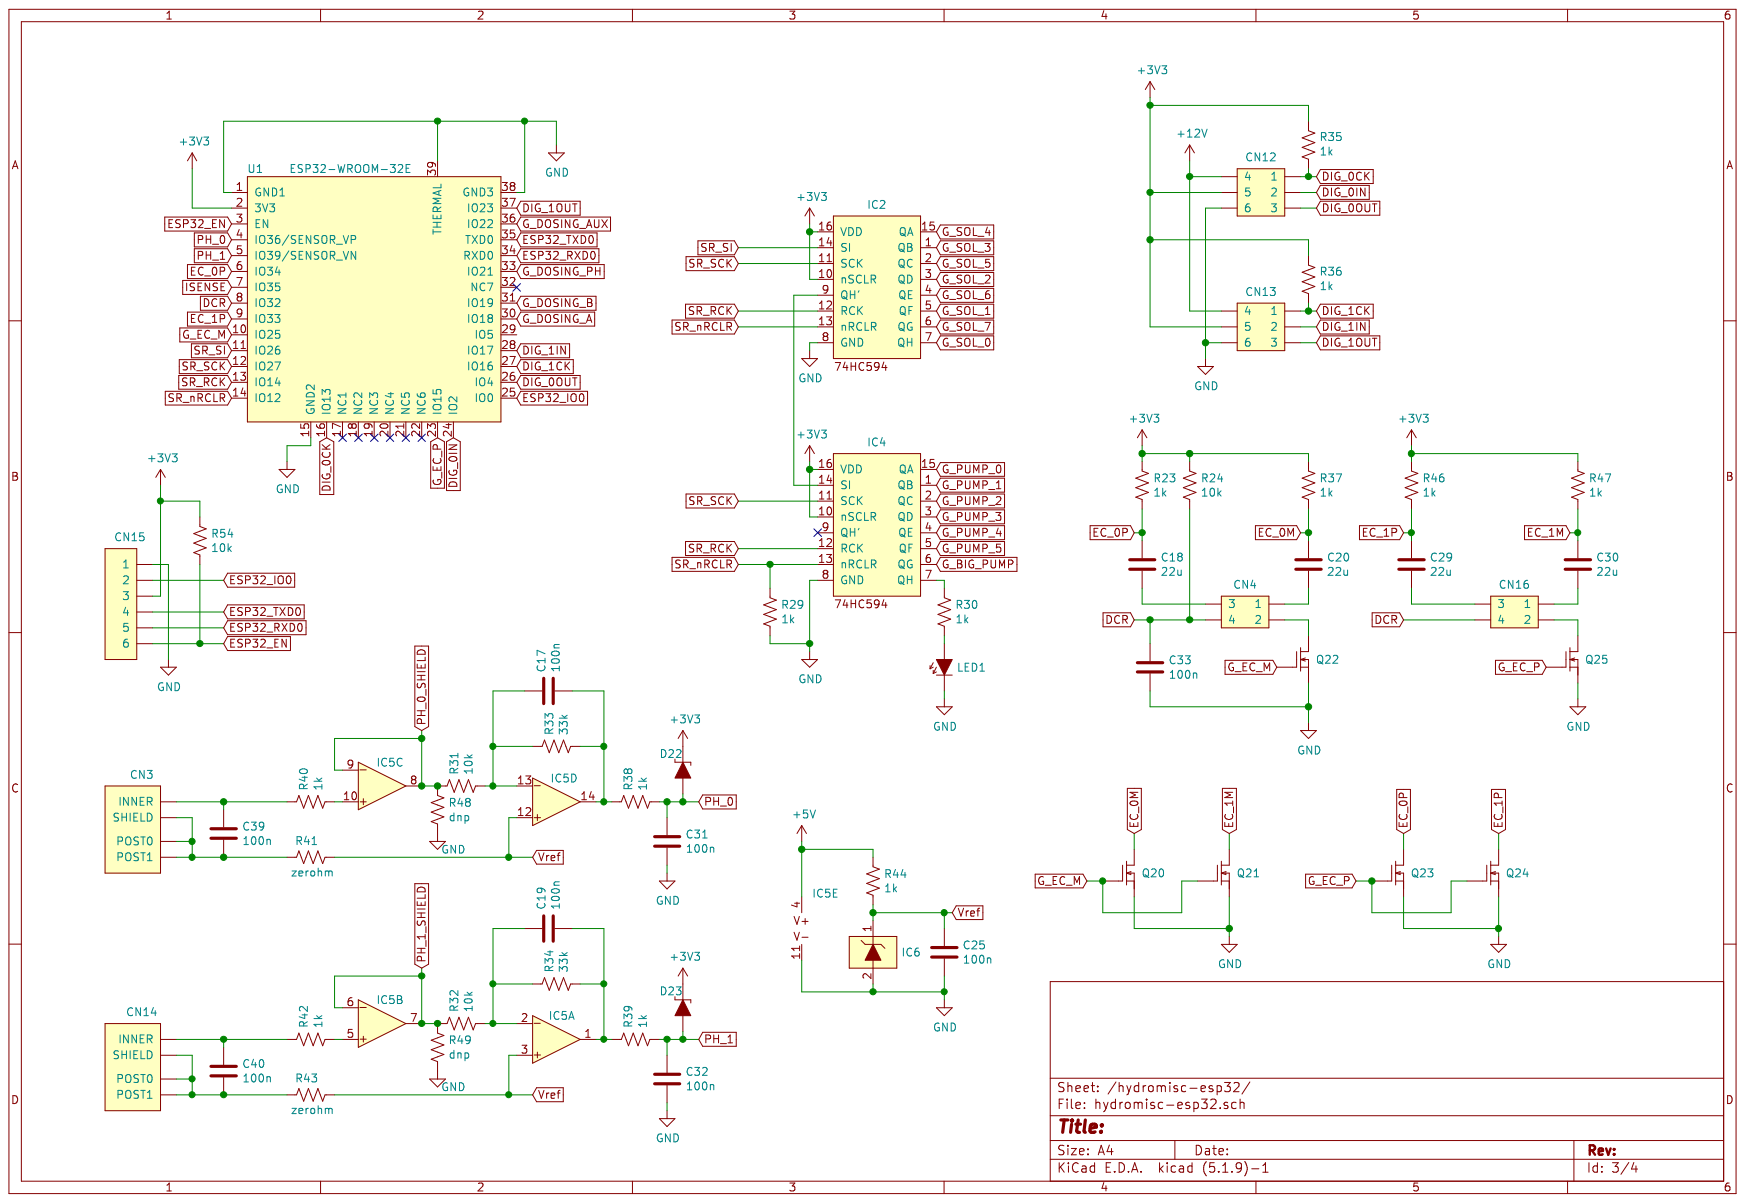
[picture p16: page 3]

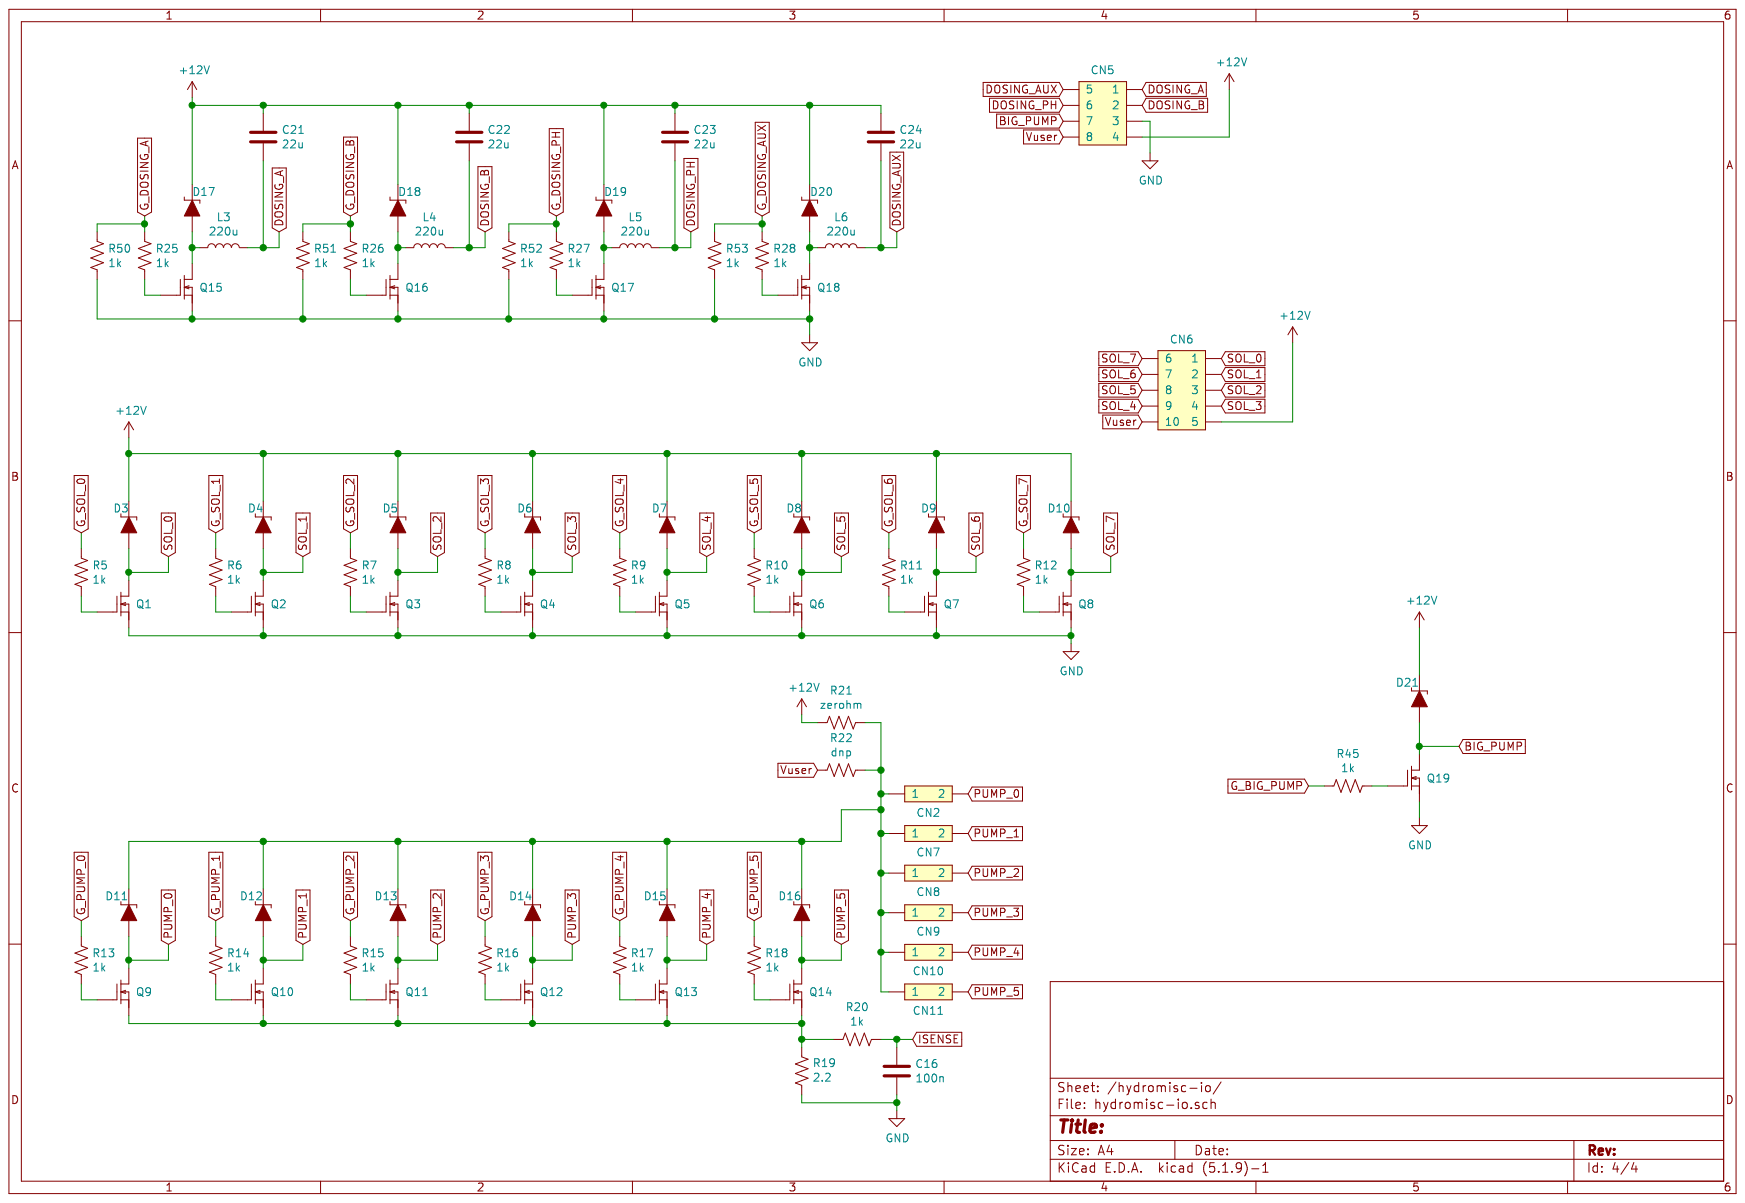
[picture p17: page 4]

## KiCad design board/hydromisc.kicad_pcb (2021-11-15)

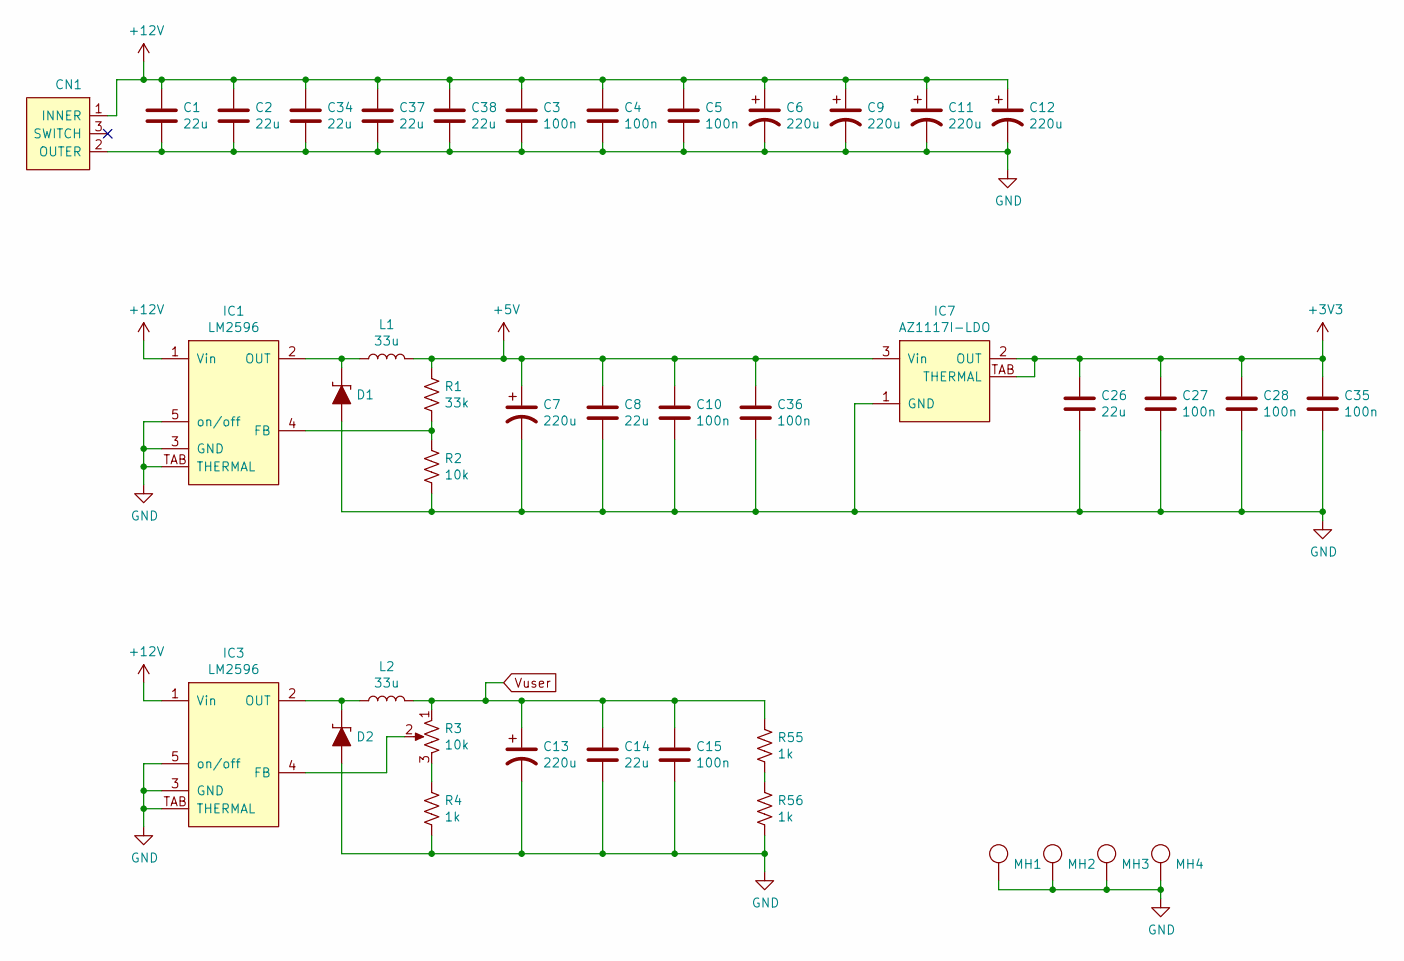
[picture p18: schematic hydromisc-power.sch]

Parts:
C1, C2, C8, C14, C26, C34, C37, C38: 22u; HM_1206
C3, C4, C5, C10, C15, C27, C28, C35, C36: 100n; HM_0603
C6, C7, C9, C11, C12, C13: 220u; HM_C_8MM_3.5MM
CN1: DC_COAX_POWER_NO_SHIELD; HM_DC_COAX_POWER_PJ-102AH
D1, D2: diode-schottky; HM_DIODE_SMB
IC1, IC3: LM2596; HM_TO-263-5
IC7: AZ1117I-LDO; HM_SOT-223
L1, L2: 33u; HM_L_SUMIDA_104CDMCCDS
MH1, MH2, MH3, MH4: MOUNTING_HOLE; HM_MOUNTING_HOLE_6MM_3MM
R1: 33k; HM_0603
R2: 10k; HM_0603
R3: 10k; HM_TRIMPOT_AB_HA06
R4, R55, R56: 1k; HM_0603

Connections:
+3V3: C26.1, C27.1, C28.1, C35.1, IC7.2 (OUT), IC7.TAB (THERMAL); also elsewhere on the board
+5V: C7.1, C8.1, C10.1, C36.1, IC7.3 (Vin), L1.2, R1.1; also elsewhere on the board
+12V: C1.1, C2.1, C3.1, C4.1, C5.1, C6.1, C9.1, C11.1, C12.1, C34.1, C37.1, C38.1, CN1.1 (INNER), IC1.1 (Vin), IC3.1 (Vin); also elsewhere on the board
GND: C1.2, C2.2, C3.2, C4.2, C5.2, C6.2, C7.2, C8.2, C9.2, C10.2, C11.2, C12.2, C13.2, C14.2, C15.2, C26.2, C27.2, C28.2, C34.2, C35.2, C36.2, C37.2, C38.2, CN1.2 (OUTER), D1.A, D2.A, IC1.3 (GND), IC1.5 (on/off), IC1.TAB (THERMAL), IC3.3 (GND), IC3.5 (on/off), IC3.TAB (THERMAL), IC7.1 (GND), MH1.1, MH2.1, MH3.1, MH4.1, R2.2, R4.2, R56.2; also elsewhere on the board
unnamed: D1.K, IC1.2 (OUT), L1.1
unnamed: D2.K, IC3.2 (OUT), L2.1
unnamed: IC1.4 (FB), R1.2, R2.1
unnamed: IC3.4 (FB), R3.2
unnamed: R3.3, R4.1
unnamed: R55.2, R56.1
Vuser: C13.1, C14.1, C15.1, L2.2, R3.1, R55.1; also elsewhere on the board

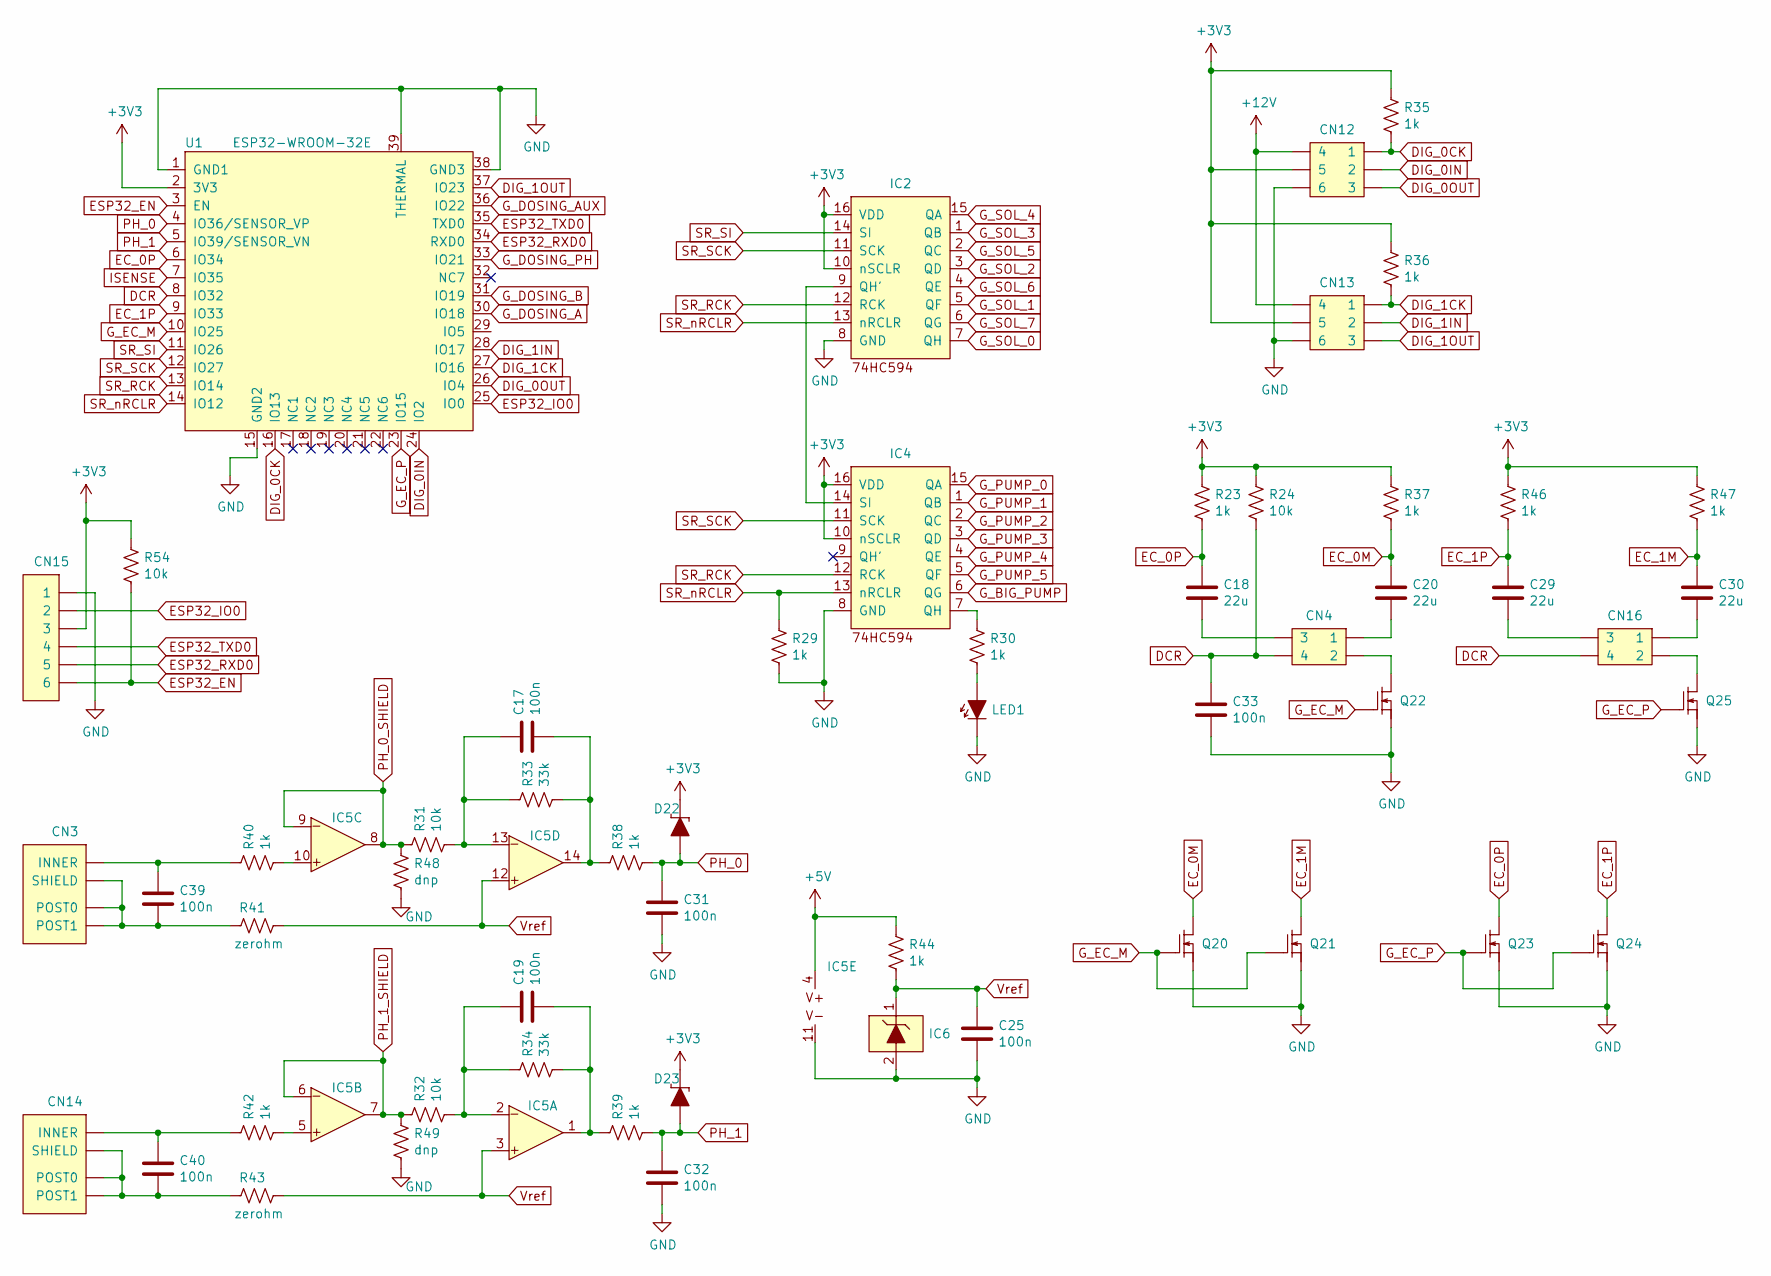
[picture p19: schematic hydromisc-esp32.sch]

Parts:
C17, C19, C25, C31, C32, C33, C39, C40: 100n; HM_0603
C18, C20, C29, C30: 22u; HM_1206
CN3, CN14: COAX_CONNECTOR; HM_BNC_MOLEX_TH_RA
CN4, CN16: MOLEX_2x2; HM_MOLEX_172448_2x2
CN12, CN13: MOLEX_2x3; HM_MOLEX_172448_2x3
CN15: HEADER_6; HM_HEADER_6_0.100_INCH
D22, D23: diode-schottky; HM_SOD-123
IC2, IC4: 74HC594; HM_SOIC-16
IC5: opamp; HM_SOIC-14
IC6: vref-diode; HM_SOT-23_123
LED1: diode-led; HM_LED_CUBE_3MM
Q20, Q21, Q22, Q23, Q24, Q25: NFET; HM_SOT-23_123
R23, R29, R30, R35, R36, R37, R38, R39, R40, R42, R44, R46, R47: 1k; HM_0603
R24, R31, R32, R54: 10k; HM_0603
R33, R34: 33k; HM_0603
R41, R43: zerohm; HM_0603
R48, R49: dnp; HM_0603
U1: ESP32-WROOM-32E; HM_ESP32-WROOM-32E

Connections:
+3V3: CN12.5, CN13.5, CN15.3, D22.K, D23.K, IC2.10 (nSCLR), IC2.16 (VDD), IC4.10 (nSCLR), IC4.16 (VDD), R23.1, R24.1, R35.2, R36.2, R37.1, R46.1, R47.1, R54.1, U1.2 (3V3); also elsewhere on the board
+5V: IC5.4 (V+), R44.1; also elsewhere on the board
+12V: CN12.4, CN13.4; also elsewhere on the board
DCR: C33.1, CN4.4, CN16.4, R24.2, U1.8 (IO32)
DIG_0CK: CN12.1, R35.1, U1.16 (IO13)
DIG_0IN: CN12.2, U1.24 (IO2)
DIG_0OUT: CN12.3, U1.26 (IO4)
DIG_1CK: CN13.1, R36.1, U1.27 (IO16)
DIG_1IN: CN13.2, U1.28 (IO17)
DIG_1OUT: CN13.3, U1.37 (IO23)
EC_0M: C20.1, Q20.3 (D), R37.2
EC_0P: C18.1, Q23.3 (D), R23.2, U1.6 (IO34)
EC_1M: C30.1, Q21.3 (D), R47.2
EC_1P: C29.1, Q24.3 (D), R46.2, U1.9 (IO33)
ESP32_EN: CN15.6, R54.2, U1.3 (EN)
ESP32_IO0: CN15.2, U1.25 (IO0)
ESP32_RXD0: CN15.5, U1.34 (RXD0)
ESP32_TXD0: CN15.4, U1.35 (TXD0)
GND: C25.2, C31.2, C32.2, C33.2, CN12.6, CN13.6, CN15.1, IC2.8 (GND), IC4.8 (GND), IC5.11 (V-), IC6.2 (-), LED1.K, Q20.2 (S), Q21.2 (S), Q22.2 (S), Q23.2 (S), Q24.2 (S), Q25.2 (S), R29.2, R48.2, R49.2, U1.1 (GND1), U1.15 (GND2), U1.38 (GND3), U1.39 (THERMAL); also elsewhere on the board
G_BIG_PUMP: IC4.6 (QG); also elsewhere on the board
G_DOSING_A: U1.30 (IO18); also elsewhere on the board
G_DOSING_AUX: U1.36 (IO22); also elsewhere on the board
G_DOSING_B: U1.31 (IO19); also elsewhere on the board
G_DOSING_PH: U1.33 (IO21); also elsewhere on the board
G_EC_M: Q20.1 (G), Q21.1 (G), Q22.1 (G), U1.10 (IO25)
G_EC_P: Q23.1 (G), Q24.1 (G), Q25.1 (G), U1.23 (IO15)
G_PUMP_0: IC4.15 (QA); also elsewhere on the board
G_PUMP_1: IC4.1 (QB); also elsewhere on the board
G_PUMP_2: IC4.2 (QC); also elsewhere on the board
G_PUMP_3: IC4.3 (QD); also elsewhere on the board
G_PUMP_4: IC4.4 (QE); also elsewhere on the board
G_PUMP_5: IC4.5 (QF); also elsewhere on the board
G_SOL_0: IC2.7 (QH); also elsewhere on the board
G_SOL_1: IC2.5 (QF); also elsewhere on the board
G_SOL_2: IC2.3 (QD); also elsewhere on the board
G_SOL_3: IC2.1 (QB); also elsewhere on the board
G_SOL_4: IC2.15 (QA); also elsewhere on the board
G_SOL_5: IC2.2 (QC); also elsewhere on the board
G_SOL_6: IC2.4 (QE); also elsewhere on the board
G_SOL_7: IC2.6 (QG); also elsewhere on the board
ISENSE: U1.7 (IO35); also elsewhere on the board
unnamed: C17.1, IC5.13 (D-), R31.2, R33.1
unnamed: C17.2, IC5.14 (DOUT), R33.2, R38.1
unnamed: C18.2, CN4.3
unnamed: C19.1, IC5.2 (A-), R32.2, R34.1
unnamed: C19.2, IC5.1 (AOUT), R34.2, R39.1
unnamed: C20.2, CN4.1
unnamed: C29.2, CN16.3
unnamed: C30.2, CN16.1
unnamed: C39.1, CN3.INNER, R40.1
unnamed: C39.2, CN3.POST0, CN3.POST1, CN3.SHIELD, R41.1
unnamed: C40.1, CN14.INNER, R42.1
unnamed: C40.2, CN14.POST0, CN14.POST1, CN14.SHIELD, R43.1
unnamed: CN4.2, Q22.3 (D)
unnamed: CN16.2, Q25.3 (D)
unnamed: IC2.9 (QH'), IC4.14 (SI)
unnamed: IC4.7 (QH), R30.1
unnamed: IC5.5 (B+), R42.2
unnamed: IC5.10 (C+), R40.2
unnamed: LED1.A, R30.2
PH_0: C31.1, D22.A, R38.2, U1.4 (IO36/SENSOR_VP)
PH_0_SHIELD: IC5.8 (COUT), IC5.9 (C-), R31.1, R48.1
PH_1: C32.1, D23.A, R39.2, U1.5 (IO39/SENSOR_VN)
PH_1_SHIELD: IC5.6 (B-), IC5.7 (BOUT), R32.1, R49.1
SR_RCK: IC2.12 (RCK), IC4.12 (RCK), U1.13 (IO14)
SR_SCK: IC2.11 (SCK), IC4.11 (SCK), U1.12 (IO27)
SR_SI: IC2.14 (SI), U1.11 (IO26)
SR_nRCLR: IC2.13 (nRCLR), IC4.13 (nRCLR), R29.1, U1.14 (IO12)
Vref: C25.1, IC5.3 (A+), IC5.12 (D+), IC6.1 (+), R41.2, R43.2, R44.2

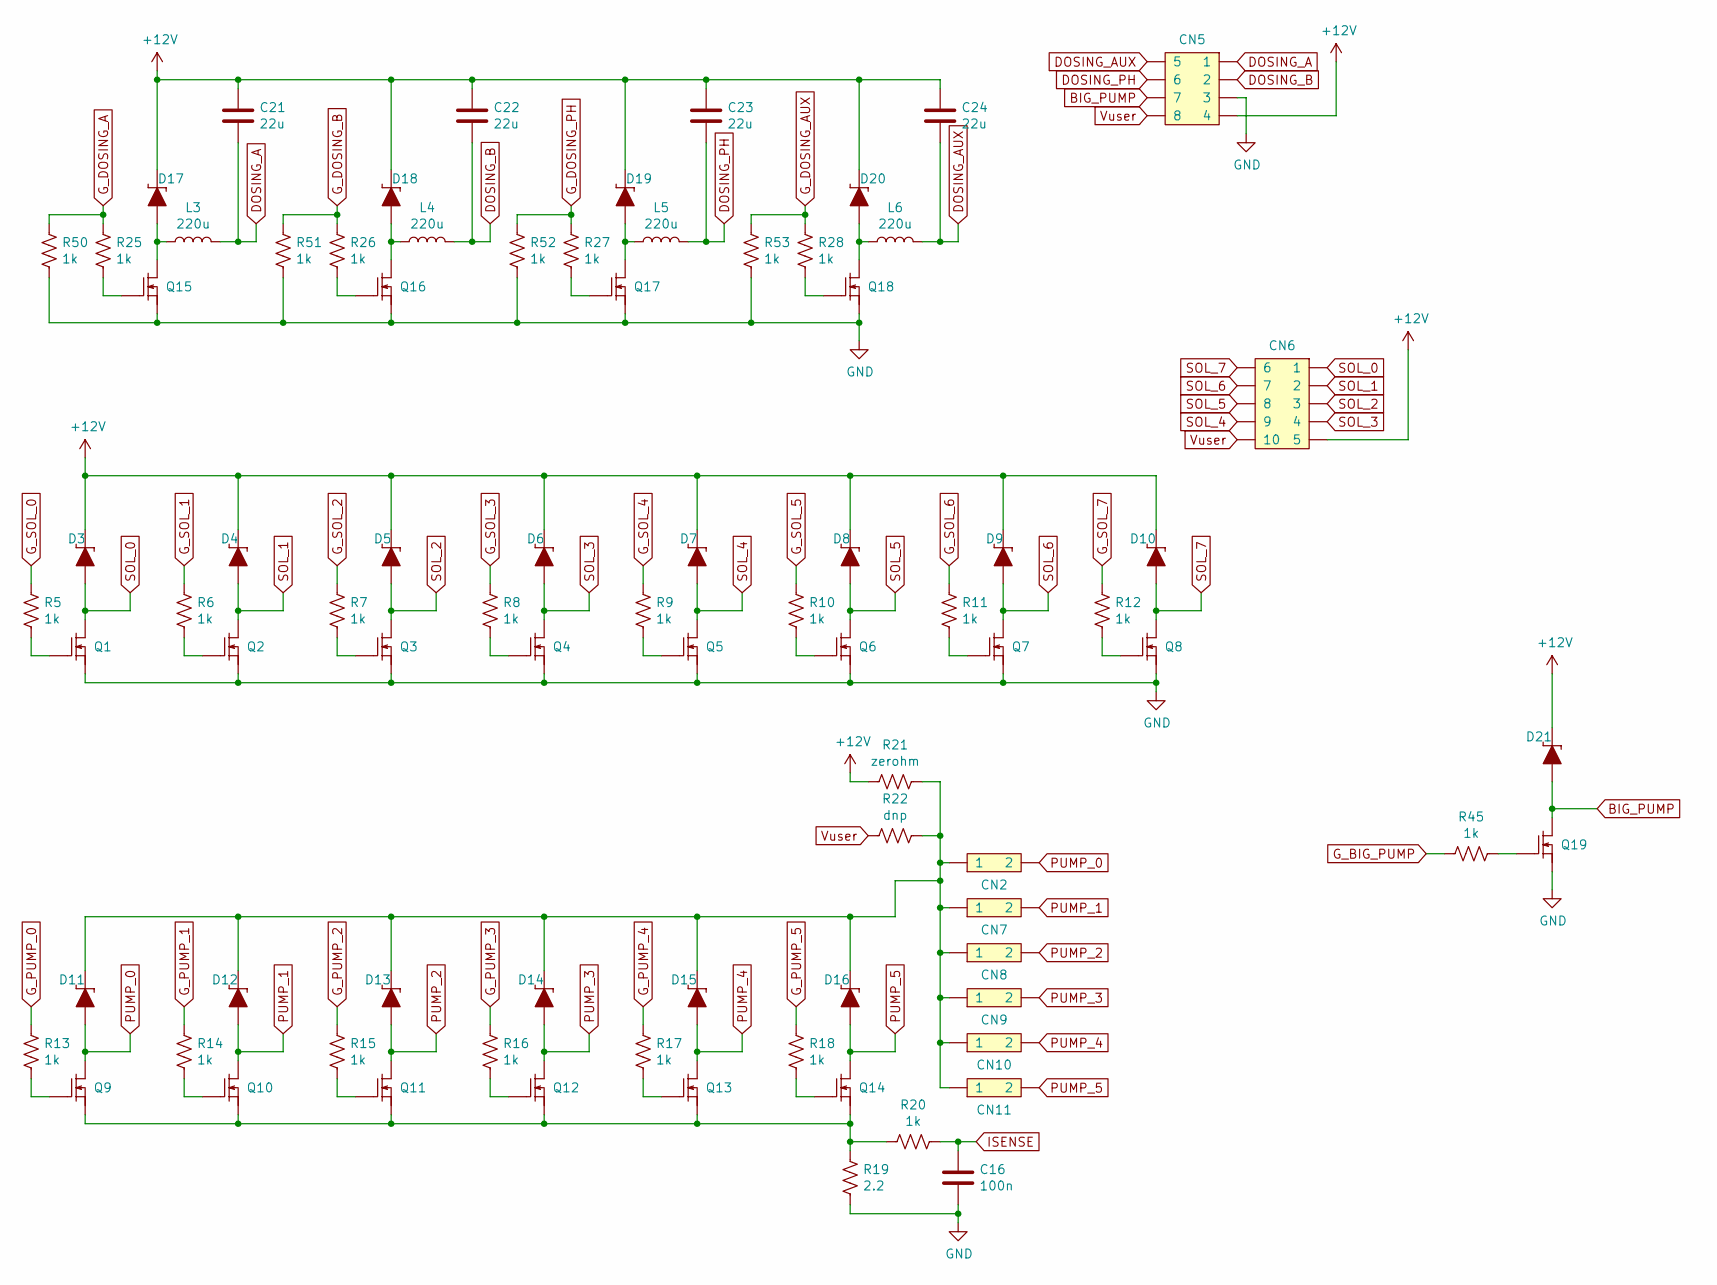
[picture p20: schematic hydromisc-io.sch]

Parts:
C16: 100n; HM_0603
C21, C22, C23, C24: 22u; HM_1206
CN2, CN7, CN8, CN9, CN10, CN11: MOLEX_2x1; HM_MOLEX_172448_2x1
CN5: MOLEX_2x4; HM_MOLEX_172448_2x4
CN6: MOLEX_2x5; HM_MOLEX_172448_2x5
D3, D4, D5, D6, D7, D8, D9, D10, D11, D12, D13, D14, D15, D16, D17, D18, D19, D20, D21: diode-schottky; HM_SOD-123
L3, L4, L5, L6: 220u; HM_L_MURATA_LQH44
Q1, Q2, Q3, Q4, Q5, Q6, Q7, Q8, Q9, Q10, Q11, Q12, Q13, Q14, Q15, Q16, Q17, Q18, Q19: NFET; HM_SOT-23_123
R5, R6, R7, R8, R9, R10, R11, R12, R13, R14, R15, R16, R17, R18, R20, R25, R26, R27, R28, R45, R50, R51, R52, R53: 1k; HM_0603
R19: 2.2; HM_2010
R21: zerohm; HM_1206
R22: dnp; HM_1206

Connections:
+12V: C21.1, C22.1, C23.1, C24.1, CN5.4, CN6.5, D3.K, D4.K, D5.K, D6.K, D7.K, D8.K, D9.K, D10.K, D17.K, D18.K, D19.K, D20.K, D21.K, R21.2; also elsewhere on the board
BIG_PUMP: CN5.7, D21.A, Q19.3 (D)
DOSING_A: C21.2, CN5.1, L3.2
DOSING_AUX: C24.2, CN5.5, L6.2
DOSING_B: C22.2, CN5.2, L4.2
DOSING_PH: C23.2, CN5.6, L5.2
GND: C16.2, CN5.3, Q1.2 (S), Q2.2 (S), Q3.2 (S), Q4.2 (S), Q5.2 (S), Q6.2 (S), Q7.2 (S), Q8.2 (S), Q15.2 (S), Q16.2 (S), Q17.2 (S), Q18.2 (S), Q19.2 (S), R19.1, R50.2, R51.2, R52.2, R53.2; also elsewhere on the board
G_BIG_PUMP: R45.2; also elsewhere on the board
G_DOSING_A: R25.1, R50.1; also elsewhere on the board
G_DOSING_AUX: R28.1, R53.1; also elsewhere on the board
G_DOSING_B: R26.1, R51.1; also elsewhere on the board
G_DOSING_PH: R27.1, R52.1; also elsewhere on the board
G_PUMP_0: R13.1; also elsewhere on the board
G_PUMP_1: R14.1; also elsewhere on the board
G_PUMP_2: R15.1; also elsewhere on the board
G_PUMP_3: R16.1; also elsewhere on the board
G_PUMP_4: R17.1; also elsewhere on the board
G_PUMP_5: R18.1; also elsewhere on the board
G_SOL_0: R5.1; also elsewhere on the board
G_SOL_1: R6.1; also elsewhere on the board
G_SOL_2: R7.1; also elsewhere on the board
G_SOL_3: R8.1; also elsewhere on the board
G_SOL_4: R9.1; also elsewhere on the board
G_SOL_5: R10.1; also elsewhere on the board
G_SOL_6: R11.1; also elsewhere on the board
G_SOL_7: R12.1; also elsewhere on the board
ISENSE: C16.1, R20.1; also elsewhere on the board
unnamed: CN2.1, CN7.1, CN8.1, CN9.1, CN10.1, CN11.1, D11.K, D12.K, D13.K, D14.K, D15.K, D16.K, R21.1, R22.1
unnamed: D17.A, L3.1, Q15.3 (D)
unnamed: D18.A, L4.1, Q16.3 (D)
unnamed: D19.A, L5.1, Q17.3 (D)
unnamed: D20.A, L6.1, Q18.3 (D)
unnamed: Q1.1 (G), R5.2
unnamed: Q2.1 (G), R6.2
unnamed: Q3.1 (G), R7.2
unnamed: Q4.1 (G), R8.2
unnamed: Q5.1 (G), R9.2
unnamed: Q6.1 (G), R10.2
unnamed: Q7.1 (G), R11.2
unnamed: Q8.1 (G), R12.2
unnamed: Q9.1 (G), R13.2
unnamed: Q10.1 (G), R14.2
unnamed: Q9.2 (S), Q10.2 (S), Q11.2 (S), Q12.2 (S), Q13.2 (S), Q14.2 (S), R19.2, R20.2
unnamed: Q11.1 (G), R15.2
unnamed: Q12.1 (G), R16.2
unnamed: Q13.1 (G), R17.2
unnamed: Q14.1 (G), R18.2
unnamed: Q15.1 (G), R25.2
unnamed: Q16.1 (G), R26.2
unnamed: Q17.1 (G), R27.2
unnamed: Q18.1 (G), R28.2
unnamed: Q19.1 (G), R45.1
PUMP_0: CN2.2, D11.A, Q9.3 (D)
PUMP_1: CN7.2, D12.A, Q10.3 (D)
PUMP_2: CN8.2, D13.A, Q11.3 (D)
PUMP_3: CN9.2, D14.A, Q12.3 (D)
PUMP_4: CN10.2, D15.A, Q13.3 (D)
PUMP_5: CN11.2, D16.A, Q14.3 (D)
SOL_0: CN6.1, D3.A, Q1.3 (D)
SOL_1: CN6.2, D4.A, Q2.3 (D)
SOL_2: CN6.3, D5.A, Q3.3 (D)
SOL_3: CN6.4, D6.A, Q4.3 (D)
SOL_4: CN6.9, D7.A, Q5.3 (D)
SOL_5: CN6.8, D8.A, Q6.3 (D)
SOL_6: CN6.7, D9.A, Q7.3 (D)
SOL_7: CN6.6, D10.A, Q8.3 (D)
Vuser: CN5.8, CN6.10, R22.2; also elsewhere on the board

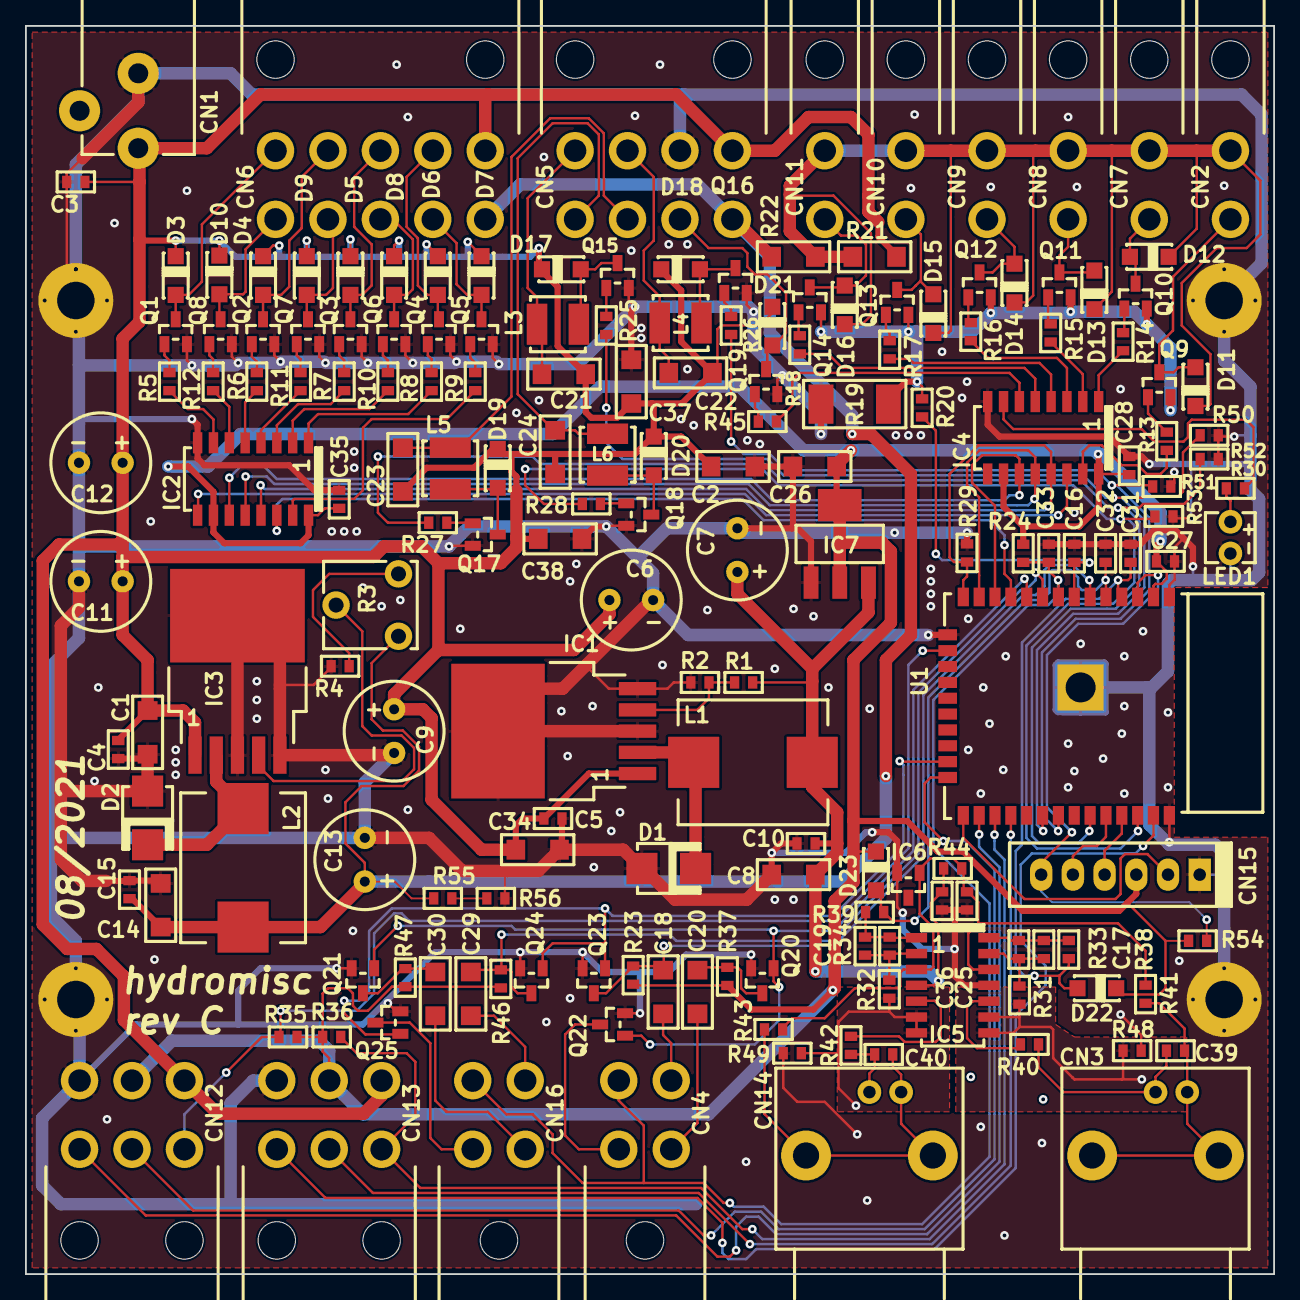
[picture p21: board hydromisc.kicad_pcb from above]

Board: 2 copper layers, 100.0 x 100.0 mm, 179 parts (0 on the bottom side), 120 nets.

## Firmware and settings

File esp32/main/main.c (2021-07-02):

/***********
 * Hydromisc, an interface to various sensors and actuators useful when
 * working with water, designed primarily for hydroponics but maybe also
 * useful for aquaria, ponds, etc. This can measure pH and EC, drive
 * solenoid valves, drive dosing pumps, drive other pumps, etc.
 *
 * Copyright 2021 Hydromisc contributors.
 *
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
 * You should have received a copy of the GNU General Public License
 * along with this program.  If not, see <http://www.gnu.org/licenses/>.
 ***********/

static const char *TAG = "hydromisc";

#include <esp_wifi.h>
#include <esp_event.h>
#include <esp_log.h>
#include <esp_system.h>
#include <nvs_flash.h>
#include <sys/param.h>
#include "esp32/rom/ets_sys.h"
#include "nvs_flash.h"
#include "esp_netif.h"
#include "esp_eth.h"
#include "esp_http_server.h"

#include "protocol_examples_common.h"

#include "driver/gpio.h"
#include "driver/ledc.h"
#include "driver/periph_ctrl.h"
#include "driver/timer.h"
#include "driver/adc.h"
#include "esp_adc_cal.h"


// GPIO assignment
//
#define GPIO_PH_0_SENSE                 36
#define ADC_PH_0_SENSE                  ADC_CHANNEL_0
#define GPIO_PH_1_SENSE                 39
#define ADC_PH_1_SENSE                  ADC_CHANNEL_3

#define GPIO_EC_0_SENSE                 34
#define ADC_EC_0_SENSE                  ADC_CHANNEL_6
#define GPIO_EC_1_SENSE                 33
#define ADC_EC_1_SENSE                  ADC_CHANNEL_5

#define GPIO_CURRENT_SENSE              35
#define ADC_CURRENT_SENSE               ADC_CHANNEL_7

#define GPIO_DCR_SENSE                  32
#define ADC_DCR_SENSE                   ADC_CHANNEL_4

#define GPIO_EC_M_GATE                  25
#define GPIO_SR_SI                      26
#define GPIO_SR_SCK                     27
#define GPIO_SR_RCK                     14
#define GPIO_SR_nRCLR                   12

#define GPIO_DIG_0_CK                   13
#define GPIO_EC_P_GATE                  15
#define GPIO_DIG_0_IN                    2
#define GPIO_DIG_0_OUT                   4
#define GPIO_DIG_1_CK                   16
#define GPIO_DIG_1_IN                   17
#define GPIO_DIG_1_OUT                  23

#define GPIO_DOSING_GATE_A              18
#define GPIO_DOSING_GATE_B              19
#define GPIO_DOSING_GATE_PH             21
#define GPIO_DOSING_GATE_AUX            22
#define LEDC_CHANNEL_DOSING_A            0
#define LEDC_CHANNEL_DOSING_B            1
#define LEDC_CHANNEL_DOSING_PH           2
#define LEDC_CHANNEL_DOSING_AUX          3


// Shift register output expander assignment

#define SR_SOLENOID_4                    0
#define SR_SOLENOID_3                    1
#define SR_SOLENOID_5                    2
#define SR_SOLENOID_2                    3
#define SR_SOLENOID_6                    4
#define SR_SOLENOID_1                    5
#define SR_SOLENOID_7                    6
#define SR_SOLENOID_0                    7

#define SR_PUMP_0                        8
#define SR_PUMP_1                        9
#define SR_PUMP_2                       10
#define SR_PUMP_3                       11
#define SR_PUMP_4                       12
#define SR_PUMP_5                       13
#define SR_BIG_PUMP                     14
#define SR_DEBUG_LED                    15


static volatile int seconds_until_stop_pump = 0;
static volatile int seconds_until_stop_solenoid = 0;
static volatile int seconds_until_stop_solenoid_pumps = 0;

static volatile int pwm_a_duty = 0,
                    pwm_b_duty = 0,
                    pwm_ph_duty = 0,
                    pwm_aux_duty = 0;

static volatile int pwm_a_phase = 0xfff,
                    pwm_b_phase = 0xfff,
                    pwm_ph_phase = 0xfff,
                    pwm_aux_phase = 0xfff;

static volatile int run_big_pump = 1;

static volatile int sr_bits = 0;

#define MAX_PUMP_PERIOD 1000
static volatile int last_pump_current[MAX_PUMP_PERIOD+10];
static int last_pump_period = 0;

#define DEFAULT_VREF    1100 // mV
static esp_adc_cal_characteristics_t adc_chars_0db;
static esp_adc_cal_characteristics_t adc_chars_11db;


// Configure GPIO pins at startup
static void config_gpio(void)
{
    gpio_config_t io_conf;

    // Outputs
    io_conf.intr_type = GPIO_PIN_INTR_DISABLE;
    io_conf.mode = GPIO_MODE_OUTPUT;
    io_conf.pin_bit_mask = 
        (1ULL << GPIO_EC_M_GATE) |
        (1ULL << GPIO_SR_SI) |
        (1ULL << GPIO_SR_SCK) |
        (1ULL << GPIO_SR_RCK) |
        (1ULL << GPIO_SR_nRCLR) |
        (1ULL << GPIO_DIG_0_CK) |
        (1ULL << GPIO_EC_P_GATE) |
        (1ULL << GPIO_DIG_0_OUT) |
        (1ULL << GPIO_DIG_1_CK) |
        (1ULL << GPIO_DIG_1_OUT) |
        (1ULL << GPIO_DOSING_GATE_A) |
        (1ULL << GPIO_DOSING_GATE_B) |
        (1ULL << GPIO_DOSING_GATE_PH) |
        (1ULL << GPIO_DOSING_GATE_AUX);
    io_conf.pull_down_en = 0;
    io_conf.pull_up_en = 0;
    gpio_config(&io_conf);

    // Inputs, analog and digital
    io_conf.mode = GPIO_MODE_INPUT;
    io_conf.pin_bit_mask =
        (1ULL << GPIO_PH_0_SENSE) |
        (1ULL << GPIO_PH_1_SENSE) |
        (1ULL << GPIO_EC_0_SENSE) |
        (1ULL << GPIO_EC_1_SENSE) |
        (1ULL << GPIO_CURRENT_SENSE) |
        (1ULL << GPIO_DCR_SENSE) |
        (1ULL << GPIO_DIG_0_IN) |
        (1ULL << GPIO_DIG_1_IN);
    gpio_config(&io_conf);

    gpio_set_level(GPIO_EC_P_GATE, 0);
    gpio_set_level(GPIO_EC_M_GATE, 0);

    gpio_set_level(GPIO_DIG_0_CK, 0);
    gpio_set_level(GPIO_DIG_1_CK, 0);

    // used for AM2301, open drain type
    gpio_set_direction(GPIO_DIG_0_OUT, GPIO_MODE_INPUT_OUTPUT_OD);
    gpio_set_pull_mode(GPIO_DIG_0_OUT, GPIO_PULLUP_ONLY);
    gpio_set_level(GPIO_DIG_0_OUT, 1);

    gpio_set_direction(GPIO_DIG_1_OUT, GPIO_MODE_INPUT_OUTPUT_OD);
    gpio_set_pull_mode(GPIO_DIG_1_OUT, GPIO_PULLUP_ONLY);
    gpio_set_level(GPIO_DIG_1_OUT, 1);

    gpio_set_level(GPIO_SR_SI, 0);
    gpio_set_level(GPIO_SR_SCK, 0);
    gpio_set_level(GPIO_SR_RCK, 0);
    gpio_set_level(GPIO_SR_nRCLR, 0);

    adc1_config_width(ADC_WIDTH_BIT_12);
    adc1_config_channel_atten(ADC_CURRENT_SENSE, ADC_ATTEN_DB_0);
    adc1_config_channel_atten(ADC_PH_0_SENSE, ADC_ATTEN_DB_11);
    adc1_config_channel_atten(ADC_PH_1_SENSE, ADC_ATTEN_DB_11);
    adc1_config_channel_atten(ADC_EC_0_SENSE, ADC_ATTEN_DB_11);
    adc1_config_channel_atten(ADC_EC_1_SENSE, ADC_ATTEN_DB_11);
    adc1_config_channel_atten(ADC_DCR_SENSE, ADC_ATTEN_DB_11);

    esp_adc_cal_characterize(ADC_UNIT_1, ADC_ATTEN_DB_0, ADC_WIDTH_BIT_12,
            DEFAULT_VREF, &adc_chars_0db);
    esp_adc_cal_characterize(ADC_UNIT_1, ADC_ATTEN_DB_11, ADC_WIDTH_BIT_12,
            DEFAULT_VREF, &adc_chars_11db);
}

static void config_ledc(void)
{
    ledc_timer_config_t ledc_timer = {
        .duty_resolution = LEDC_TIMER_8_BIT,
        .freq_hz = 300000,
        .speed_mode = LEDC_LOW_SPEED_MODE,
        .timer_num = LEDC_TIMER_1,
        .clk_cfg = LEDC_AUTO_CLK,
    };
    ledc_timer_config(&ledc_timer);

    ledc_timer.speed_mode = LEDC_HIGH_SPEED_MODE;
    ledc_timer.timer_num = LEDC_TIMER_0;
    ledc_timer_config(&ledc_timer);

    ledc_channel_config_t ch_a = {
        .channel    = LEDC_CHANNEL_DOSING_A,
        .duty       = 0,
        .gpio_num   = GPIO_DOSING_GATE_A,
        .speed_mode = LEDC_HIGH_SPEED_MODE,
        .hpoint     = 0,
        .timer_sel  = LEDC_TIMER_0
    };
    ledc_channel_config(&ch_a);

    ledc_channel_config_t ch_b = {
        .channel    = LEDC_CHANNEL_DOSING_B,
        .duty       = 0,
        .gpio_num   = GPIO_DOSING_GATE_B,
        .speed_mode = LEDC_HIGH_SPEED_MODE,
        .hpoint     = 0,
        .timer_sel  = LEDC_TIMER_0
    };
    ledc_channel_config(&ch_b);

    ledc_channel_config_t ch_ph = {
        .channel    = LEDC_CHANNEL_DOSING_PH,
        .duty       = 0,
        .gpio_num   = GPIO_DOSING_GATE_PH,
        .speed_mode = LEDC_HIGH_SPEED_MODE,
        .hpoint     = 0,
        .timer_sel  = LEDC_TIMER_0
    };
    ledc_channel_config(&ch_ph);

    ledc_channel_config_t ch_aux = {
        .channel    = LEDC_CHANNEL_DOSING_AUX,
        .duty       = 0,
        .gpio_num   = GPIO_DOSING_GATE_AUX,
        .speed_mode = LEDC_HIGH_SPEED_MODE,
        .hpoint     = 0,
        .timer_sel  = LEDC_TIMER_0
    };
    ledc_channel_config(&ch_aux);

}

static void sr_set(int bit, int value)
{
    portDISABLE_INTERRUPTS();
    if(value) {
        sr_bits |=  (1 << bit);
    } else {
        sr_bits &= ~(1 << bit);
    }
    portENABLE_INTERRUPTS();
}

static void sr_write(void)
{
    portDISABLE_INTERRUPTS();
    int i;
    for(i = 15; i >= 0; i--) {
        gpio_set_level(GPIO_SR_SI, (sr_bits & (1 << i)) ? 1 : 0);
        ets_delay_us(1);
        gpio_set_level(GPIO_SR_SCK, 1);
        ets_delay_us(1);
        gpio_set_level(GPIO_SR_SCK, 0);
        ets_delay_us(1);
    }

    gpio_set_level(GPIO_SR_RCK, 1);
    ets_delay_us(1);
    gpio_set_level(GPIO_SR_RCK, 0);
    ets_delay_us(1);
    gpio_set_level(GPIO_SR_nRCLR, 1);
    portENABLE_INTERRUPTS();
}

static void sr_set_and_write(int bit, int value) {
    sr_set(bit, value);
    sr_write();
}

static void set_dosing_pwm(int a, int b, int ph, int aux)
{
    ledc_set_duty(LEDC_HIGH_SPEED_MODE, LEDC_CHANNEL_DOSING_A, a);
    ledc_update_duty(LEDC_HIGH_SPEED_MODE, LEDC_CHANNEL_DOSING_A);

    ledc_set_duty(LEDC_HIGH_SPEED_MODE, LEDC_CHANNEL_DOSING_B, b);
    ledc_update_duty(LEDC_HIGH_SPEED_MODE, LEDC_CHANNEL_DOSING_B);

    ledc_set_duty(LEDC_HIGH_SPEED_MODE, LEDC_CHANNEL_DOSING_PH, ph);
    ledc_update_duty(LEDC_HIGH_SPEED_MODE, LEDC_CHANNEL_DOSING_PH);

    ledc_set_duty(LEDC_HIGH_SPEED_MODE, LEDC_CHANNEL_DOSING_AUX, aux);
    ledc_update_duty(LEDC_HIGH_SPEED_MODE, LEDC_CHANNEL_DOSING_AUX);
}

static void stop_solenoid_pumps(void)
{
    sr_set(SR_BIG_PUMP, 0);

    sr_write();

    pwm_a_duty = 0;
    pwm_b_duty = 0;
    pwm_ph_duty = 0;
    pwm_aux_duty = 0;

    set_dosing_pwm(0, 0, 0, 0);

    seconds_until_stop_solenoid_pumps = 0;
}

static void stop_solenoid(void)
{
    sr_set(SR_SOLENOID_0, 0);
    sr_set(SR_SOLENOID_1, 0);
    sr_set(SR_SOLENOID_2, 0);
    sr_set(SR_SOLENOID_3, 0);
    sr_set(SR_SOLENOID_4, 0);
    sr_set(SR_SOLENOID_5, 0);
    sr_set(SR_SOLENOID_6, 0);
    sr_set(SR_SOLENOID_7, 0);

    sr_write();

    seconds_until_stop_solenoid = 0;
}

static void stop_pump(void) {
    sr_set(SR_PUMP_0, 0);
    sr_set(SR_PUMP_1, 0);
    sr_set(SR_PUMP_2, 0);
    sr_set(SR_PUMP_3, 0);
    sr_set(SR_PUMP_4, 0);
    sr_set(SR_PUMP_5, 0);

    sr_write();

    seconds_until_stop_pump = 0;
}

static void stop_everything(void)
{
    stop_solenoid();
    stop_solenoid_pumps();
    stop_pump();
}

static int start_solenoid(int k, int dosingA, int dosingB, int dosingPh, int dosingAux, int t)
{
    stop_everything();

    if(k         < 0 || k         > 7   ||
       dosingA   < 0 || dosingA   > 255 ||
       dosingB   < 0 || dosingB   > 255 ||
       dosingPh  < 0 || dosingPh  > 255 ||
       dosingAux < 0 || dosingAux > 255 ||
       t         < 5 || t         > 120)
    {
        return 0;
    }

    seconds_until_stop_solenoid_pumps = t;

    // want the pump to stop first, so we don't hold pressure
    seconds_until_stop_solenoid = t + 3;

    switch(k) {
        case 0: sr_set(SR_SOLENOID_0, 1); break;
        case 1: sr_set(SR_SOLENOID_1, 1); break;
        case 2: sr_set(SR_SOLENOID_2, 1); break;
        case 3: sr_set(SR_SOLENOID_3, 1); break;
        case 4: sr_set(SR_SOLENOID_4, 1); break;
        case 5: sr_set(SR_SOLENOID_5, 1); break;
        case 6: sr_set(SR_SOLENOID_6, 1); break;
        case 7: sr_set(SR_SOLENOID_7, 1); break;
    }

    if(run_big_pump) sr_set(SR_BIG_PUMP, 1);

    sr_set(SR_DEBUG_LED, 1);

    sr_write();

    pwm_a_duty = dosingA;
    pwm_b_duty = dosingB;
    pwm_ph_duty = dosingPh;
    pwm_aux_duty = dosingAux;

    return 1;
}

static int start_pump(int k, int t)
{
    stop_everything();

    if(k < 0 || k > 5 || t < 5 || t > MAX_PUMP_PERIOD) return 0;

    memset((void *)last_pump_current, 0, sizeof(last_pump_current));
    last_pump_period = t;

    seconds_until_stop_pump = t;

    switch(k) {
        case 0: sr_set(SR_PUMP_0, 1); break;
        case 1: sr_set(SR_PUMP_1, 1); break;
        case 2: sr_set(SR_PUMP_2, 1); break;
        case 3: sr_set(SR_PUMP_3, 1); break;
        case 4: sr_set(SR_PUMP_4, 1); break;
        case 5: sr_set(SR_PUMP_5, 1); break;
    }

    sr_set(SR_DEBUG_LED, 1);

    sr_write();

    return 1;
}

static xQueueHandle timer_tick_queue;

static void timer_tick_task(void *arg)
{
    int mod10 = 0, mod12 = 0;

    while (1) {
        int evt;
        xQueueReceive(timer_tick_queue, &evt, portMAX_DELAY);

        // software PWM with period of twelve ticks = 1200 ms
        //
        mod12++;
        if(mod12 >= 12) mod12 = 0;

        int a = 0, b = 0, ph = 0, aux = 0;
        if(pwm_a_phase   & (1 << mod12)) a   = pwm_a_duty;
        if(pwm_b_phase   & (1 << mod12)) b   = pwm_b_duty;
        if(pwm_ph_phase  & (1 << mod12)) ph  = pwm_ph_duty;
        if(pwm_aux_phase & (1 << mod12)) aux = pwm_aux_duty;
        set_dosing_pwm(a, b, ph, aux);
        
        // and timeout with period of ten ticks = 1 s

        mod10++;
        if(mod10 < 10) continue;
        mod10 = 0;

        if(seconds_until_stop_pump > 0) {
            seconds_until_stop_pump--;

            int i, v = 0, n = 32;
            for(i = 0; i < n; i++) {
                v += adc1_get_raw(ADC_CURRENT_SENSE);
            }
            v /= n;
            // 2.2 ohm sense resistor
            v = (int)(esp_adc_cal_raw_to_voltage(v, &adc_chars_0db) / 2.2f);

            last_pump_current[seconds_until_stop_pump] = v;

            if(seconds_until_stop_pump == 0) {
                ESP_LOGI(TAG, "TICK => pump stop next tick");
                sr_set(SR_DEBUG_LED, 0); // to write later
            }
        } else {
            stop_pump();
        }

        if(seconds_until_stop_solenoid_pumps > 0) {
            seconds_until_stop_solenoid_pumps--;
            if(seconds_until_stop_solenoid_pumps == 0) {
                ESP_LOGI(TAG, "TICK => solenoid pumps stop next tick");
                sr_set(SR_DEBUG_LED, 0); // to write later
            }
        } else {
            stop_solenoid_pumps();
        }

        if(seconds_until_stop_solenoid > 0) {
            seconds_until_stop_solenoid--;
            if(seconds_until_stop_solenoid == 0) {
                ESP_LOGI(TAG, "TICK => solenoid stop next tick");
                sr_set(SR_DEBUG_LED, 0); // to write later
            }
        } else {
            stop_solenoid();
        }
    }
}

void IRAM_ATTR timer_tick_isr(void *param)
{
    timer_spinlock_take(TIMER_GROUP_0);

    timer_group_clr_intr_status_in_isr(TIMER_GROUP_0, TIMER_0);
    timer_group_enable_alarm_in_isr(TIMER_GROUP_0, TIMER_0);

    int evt = 0;
    xQueueSendFromISR(timer_tick_queue, &evt, NULL);

    timer_spinlock_give(TIMER_GROUP_0);
}

static void config_timer_tick(void)
{
    timer_tick_queue = xQueueCreate(10, sizeof(int));

    xTaskCreate(timer_tick_task, "timer_evt_task", 2048, NULL, 5, NULL);

    timer_config_t config = {
        .divider = 16,
        .counter_dir = TIMER_COUNT_UP,
        .counter_en = TIMER_PAUSE,
        .alarm_en = TIMER_ALARM_EN,
        .auto_reload = true,
    };
    timer_init(TIMER_GROUP_0, TIMER_0, &config);

    timer_set_counter_value(TIMER_GROUP_0, TIMER_0, 0ULL);

    timer_set_alarm_value(TIMER_GROUP_0, TIMER_0, (TIMER_BASE_CLK / (16*10)));
    timer_enable_intr(TIMER_GROUP_0, TIMER_0);
    timer_isr_register(TIMER_GROUP_0, TIMER_0, timer_tick_isr, NULL,
                                                    ESP_INTR_FLAG_IRAM, NULL);

    timer_start(TIMER_GROUP_0, TIMER_0);
}

static void send_response(httpd_req_t *req, const char *resp_str) {
    httpd_resp_set_hdr(req, "Access-Control-Allow-Origin", "*");
    httpd_resp_send(req, resp_str, strlen(resp_str));
}

static esp_err_t solenoid_get_handler(httpd_req_t *req)
{
    char*  buf;
    size_t buf_len;
    int ok = 0;

    buf_len = httpd_req_get_url_query_len(req) + 1;
    if (buf_len > 1) {
        buf = malloc(buf_len);
        if (httpd_req_get_url_query_str(req, buf, buf_len) == ESP_OK) {
            char param[32];
            int k = -1, dosingA = -1, dosingB = -1, dosingPh = -1, dosingAux = -1, t = -1;

            if(httpd_query_key_value(buf, "k", param, sizeof(param)) == ESP_OK) {
                k = atoi(param);
            }
            if(httpd_query_key_value(buf, "dosingA", param, sizeof(param)) == ESP_OK) {
                dosingA = atoi(param);
            }
            if(httpd_query_key_value(buf, "dosingB", param, sizeof(param)) == ESP_OK) {
                dosingB = atoi(param);
            }
            if(httpd_query_key_value(buf, "dosingPh", param, sizeof(param)) == ESP_OK) {
                dosingPh = atoi(param);
            }
            if(httpd_query_key_value(buf, "dosingAux", param, sizeof(param)) == ESP_OK) {
                dosingAux = atoi(param);
            }
            if(httpd_query_key_value(buf, "t", param, sizeof(param)) == ESP_OK) {
                t = atoi(param);
            }

            ESP_LOGI(TAG, "FLOODING => k=%d dosingA=%d dosingB=%d dosingPh=%d dosingAux=%d t=%d", k, dosingA, dosingB, dosingPh, dosingAux, t);
            ok = start_solenoid(k, dosingA, dosingB, dosingPh, dosingAux, t);
        }
        free(buf);
    }

    const char *resp_str = ok ? "{ \"result\": \"solenoiding\" }\r\n" : "{ \"result\": \"error\" }\r\n";
    send_response(req, resp_str);

    return ESP_OK;
}

static esp_err_t pump_get_handler(httpd_req_t *req)
{
    char*  buf;
    size_t buf_len;
    int ok = 0;

    buf_len = httpd_req_get_url_query_len(req) + 1;
    if (buf_len > 1) {
        buf = malloc(buf_len);
        if (httpd_req_get_url_query_str(req, buf, buf_len) == ESP_OK) {
            char param[32];
            int k = -1, t = -1;

            if(httpd_query_key_value(buf, "k", param, sizeof(param)) == ESP_OK) {
                k = atoi(param);
            }
            if(httpd_query_key_value(buf, "t", param, sizeof(param)) == ESP_OK) {
                t = atoi(param);
            }
            ESP_LOGI(TAG, "DRAINING => k=%d t=%d", k, t);
            ok = start_pump(k, t);
        }
        free(buf);
    }

    const char *resp_str = ok ? "{ \"result\": \"pumping\" }\r\n" : "{ \"result\": \"error\" }\r\n";
    send_response(req, resp_str);

    return ESP_OK;
}

static esp_err_t stop_get_handler(httpd_req_t *req)
{
    ESP_LOGI(TAG, "STOPPING");

    stop_everything();

    send_response(req, "{ \"result\": \"stopping\" }\r\n");

    return ESP_OK;
}

static esp_err_t current_get_handler(httpd_req_t *req)
{
    ESP_LOGI(TAG, "CURRENT");

    static char resp_str[MAX_PUMP_PERIOD*6+100];
    strcpy(resp_str, "{ \"result\": \"current\", \"current\": [ ");
    int i, p = strlen(resp_str);
    for(i = last_pump_period - 1; i >= 0; i--) {
        char num[20];
        sprintf(num, "%d", last_pump_current[i]);
        num[6] = 0;
        strcpy(resp_str+p, num);
        p += strlen(num);

        if(i != 0) {
            resp_str[p++] = ',';
        }
        resp_str[p++] = ' ';
    }
    strcpy(resp_str+p, "] }\r\n");

    send_response(req, resp_str);

    return ESP_OK;
}
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
void app_main(void)
{
    static httpd_handle_t server = NULL;

    ESP_ERROR_CHECK(nvs_flash_init());
    ESP_ERROR_CHECK(esp_netif_init());
    ESP_ERROR_CHECK(esp_event_loop_create_default());

    ESP_ERROR_CHECK(example_connect());

    ESP_ERROR_CHECK(esp_event_handler_register(IP_EVENT,
                    IP_EVENT_STA_GOT_IP, &connect_handler, &server));
    ESP_ERROR_CHECK(esp_event_handler_register(WIFI_EVENT,
                    WIFI_EVENT_STA_DISCONNECTED, &disconnect_handler, &server));

    // GPIO directions and ADC pins
    config_gpio();
    // The LEDC is designed for LEDs, but we use it for dosing pump PWM
    config_ledc();
    // Periodic 100 ms tick that sequences our coarse timing
    config_timer_tick();

    // Blink LED to show we're alive
    for(int i = 0; i < 3; i++) {
        sr_set_and_write(SR_DEBUG_LED, 1);
        ets_delay_us(200*1000);
        sr_set_and_write(SR_DEBUG_LED, 0);
        ets_delay_us(200*1000);
    }

    server = start_webserver();
}

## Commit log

2021-07-02 Add labeled images of connectors.
2021-07-02 Add ESP32 firmware.
2021-07-02 Add .gitignore for ESP32 build artifacts.
2021-07-02 Add rev A schematics and layouts.
    This is tested and working, except that it's missing a pull-up on
    ESP32_EN. I'll correct this in rev B, or a 10k resistor could be
    hand-soldered from ESP32_EN to +3V3 (e.g., near CN15).
    [hydromisc-esp32.sch, hydromisc-io.sch, hydromisc-power.sch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]
2021-07-02 Update PCB to rev B.
    Add the missing pull-up on ESP32_EN, some pull-down on Vuser to
    fight off-brand LM2596 leakage current, and a README.md explaining.
    [hydromisc-esp32.sch, hydromisc-power.sch, hydromisc.kicad_pcb]
2021-07-03 Add Gerbers, BOM, and PDF schematics for rev B.
    Also fix README.md, since current spec for dosing pumps was too high,
    limited by inductor.
    [hydromisc-bill-of-materials-revB.csv]
2021-07-04 Oops, fix use of slope in pH calibration example.
    Also fix missing word, and improve introduction.
2021-08-15 Add capacitors directly across pH probes.
    This fixes a problem with 60 Hz (or 50 Hz) pickup, when the wires are
    long or the noise is coupling to the water. Also replace the 1k resistors
    to the shield with zero-ohm resistors, to further reduce that noise.
    This updates the board to rev C. Also check in PDF schematics, BOM,
    and Gerbers.
    [hydromisc-bill-of-materials-revC.csv, hydromisc-esp32.sch, hydromisc.kicad_pcb]
2021-08-25 Add images of sensors and actuators.
2021-08-25 Add review of sensors and actuators.
2021-11-15 Added SMD tag to SMD components for centroid data output.
    [hydromisc.kicad_pcb]

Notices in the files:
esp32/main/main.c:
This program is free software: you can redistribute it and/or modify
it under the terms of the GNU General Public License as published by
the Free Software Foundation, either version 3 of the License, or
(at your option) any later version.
